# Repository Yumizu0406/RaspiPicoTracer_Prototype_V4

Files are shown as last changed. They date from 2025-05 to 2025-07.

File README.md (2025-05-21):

# RaspiPicoTracer_Prototype_V4

RaspiPicoTracerは白線の上をたどって走るロボットであり、
機能をできる限り少なくし、回路、メカ、組み立て、プログラミングなどロボット作成に必要な経験を一通り短期間で行えるように開発中です。
このロボットはマイクロマウス大会のロボトレース競技に参加することを想定して作成しています。
競技の詳細はロボトレース競技規定をご確認ください。
[ロボトレース競技規程](https://www.ntf.or.jp/?page_id=68)

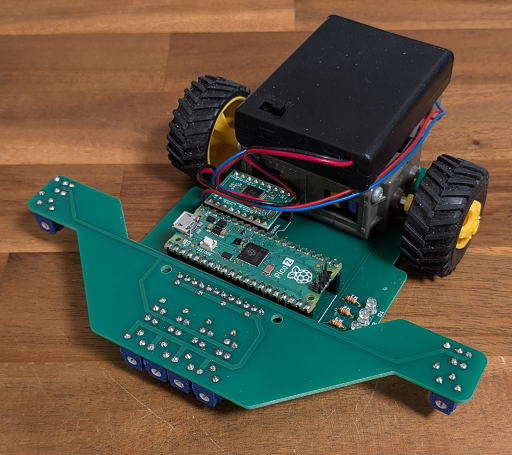
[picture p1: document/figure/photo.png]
RaspiPicoTracer_photo


<br>

# スペック
| 項目 | 詳細 |
| ---- | ---- |
| サイズ | 幅:150mm  長さ:148mm  高さ:46mm |
| 重さ | 約220g |
| 電源 | 単四電池4本 |
| モーター | FA-130 |
| モータードライバ | TB6612 |
| CPU | RP2350 |
| ラインセンサ | LBR-127HLD×4 |
| ホイール | 径:36mm 幅:16mm |

# 開発環境について
VSCodeでRaspberry Pi PicoのExtensionを使用します。
Raspberry Pi財団が公開しているドキュメント「Getting started with Raspberry Pi Pico-series」の内容に沿って行ってください。

cloneした後はImport Projectを行ってください。

# 回路図
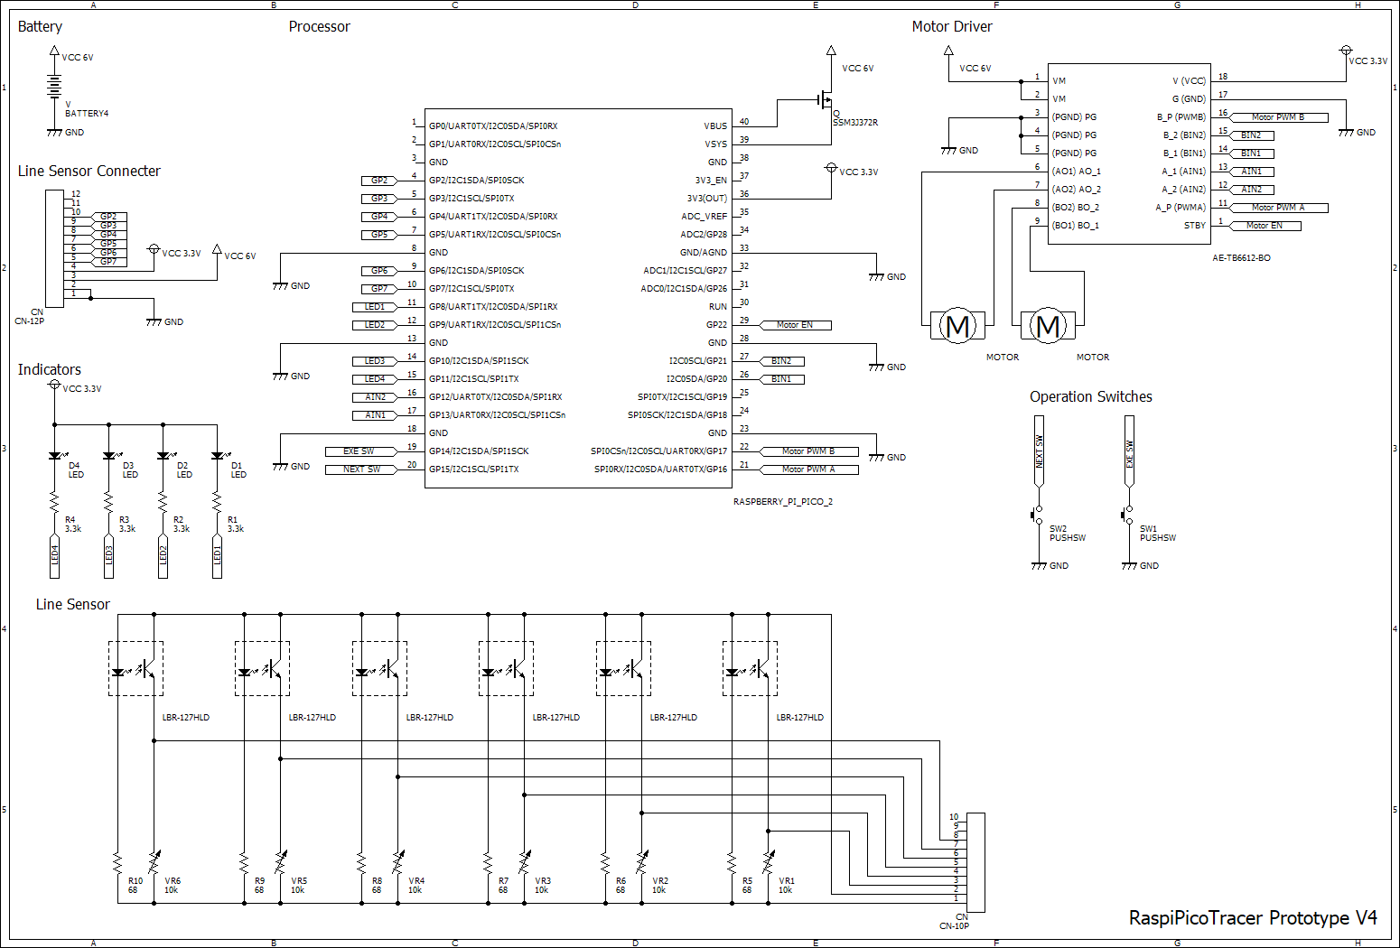
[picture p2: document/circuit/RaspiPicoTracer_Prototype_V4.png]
CircuitDiagram


# 部品表

| 名称 | メーカー | 単価 | 個数 | 備考 |
| ---- | ---- | ---- | ---- | ---- |
| メイン基板 | - | - | 1 | - |
| センサ基板 | - | - | 1 | - |
| Raspberry Pi Pico 2 | ラズベリーパイ財団 | 1000 | 1 | Raspberry Pi Picoでも可 |
| ダブルギヤボックス（左右独立４速タイプ） | 株式会社タミヤ | 924 | 1 | ギヤ比12.7:1で利用 |
| トラックタイヤセット （36mm径） | 株式会社タミヤ | 396 | 1 | - |
| 電池ボックス 単4×4本 リード線・フタ・スイッチ付 | COMFORTABLE ELECTRONIC CO., LTD(COMF) | 150 | 1 | - |
| 耐熱電子ワイヤー 黒色 20m 導体外径0.54mm(AWG24相当) | 住友電気工業株式会社 | 600 | 1 | モータードライバとモーター接続用<br>14cmのものを4つ利用 |
| TB6612モータードライバー ブレークアウトボードキット | 秋月電子 | 380 | 1 | 1 |
| LED(LC303PBL1-30Q) | - | - | 4 | 高輝度で3mm径のものならなんでもOK |
| 抵抗器 3.3kΩ | - | - | 4 | LED用 |
| ピンヘッダー 1×40 (40P) | Useconn Electronics Ltd. | 35 | 2 | - |
| 分割ロングピンソケット 1×42 (42P) | Useconn Electronics Ltd. | 80 | 2 | - |
| タクトスイッチ(DTS-63-N-V-BLK) | Cosland Co,. Ltd. | 15 | 2 | - |
| フォトリフレクター(反射型フォトセンサー) LBR-127HLD | Letex Technology Corp. | 75 | 6 | - |
| 半固定ボリューム TSR-3323S 10kΩ | SUNTAN TECHNOLOGY CO LTD | 40 | 6 | - |
| 抵抗器 68Ω | - | - | 6 | フォトリフレクター用 |

<br>

# 組み立て方法

準備として以下の工具を揃えてください。
| 名称 | 備考 |
| ---- | ---- |
| はんだごて | 15w～30wのものがよい |
| こて先クリーナー | - |
| はんだ | スズ60％ 鉛入りはんだ Φ0.8mmだとよい |
| 精密作業用ニッパー | - |
| ＋ドライバー | サイズは2番 |
| ワイヤストリッパー | あると嬉しい<br>なくてもOK |

<br>

モーターとの接続について以下の画像のように接続してください。
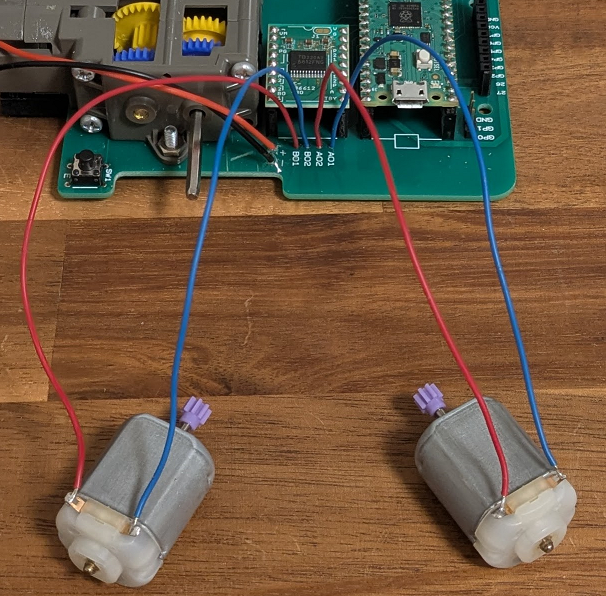
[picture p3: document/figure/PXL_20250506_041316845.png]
ConnectToMotor


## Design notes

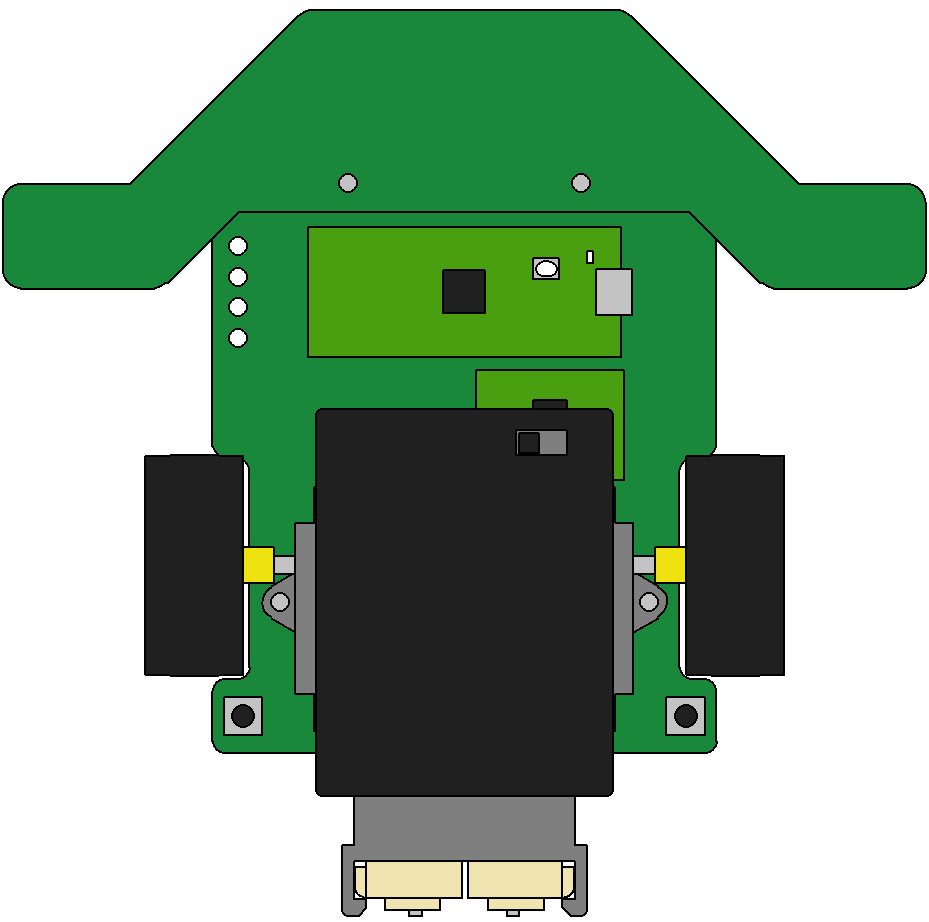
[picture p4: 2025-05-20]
document/figure/ラズピコトレーサ-.png

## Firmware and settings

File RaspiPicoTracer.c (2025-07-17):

#include <stdint.h>
#include <stdio.h>
#include "pico/stdlib.h"
#include "driver/indicators.h"
#include "driver/cycle.h"
#include "driver/sw.h"
#include "driver/lineSensor.h"
#include "driver/adchange.h"
#include "driver/TB6612FNG.h"
#include "application/control.h"
#include "application/battery_monitor.h"
#include "application/dc_motor.h"

typedef enum{
    selecting_menu = 0,
	exe_menu
}menu_status_t;

void init_driver(void);
void menu_no_0(void);
void menu_no_1(void);
void menu_no_2(void);
void menu_no_3(void);
void menu_no_4(void);
void menu_no_5(void);
void menu_no_6(void);
void menu_no_7(void);
void exe_select_func(uint8_t select_func);

static uint8_t menu_no;
static menu_status_t menu_status;

void (*ptr_f[8])(void) = {
    menu_no_0,
    menu_no_1,
    menu_no_2,
    menu_no_3,
    menu_no_4,
    menu_no_5,
    menu_no_6,
    menu_no_7
};

int main()
{
    control_parameters_t parameter;

    menu_no = 0;
    menu_status = selecting_menu;

    stdio_init_all();
    init_battery();
    init_control();

    parameter.speed_at_straight = 500;
    parameter.p_gain_at_straight = 15.0;
    set_control_parameter(trial_run, parameter);

    init_driver();
    set_speed_dc_motor(A, 1);
    set_speed_dc_motor(B, 1);

    while (true) {
        if(menu_status == selecting_menu){
            set_Raspberry_Pi_LED_mode(led_mode_switching);
            if(isSwStatus(SW_NEXT, click)){
                menu_no++;
                if(menu_no >= 8){
                    menu_no = 0;
                }
            }
            out_indicators(menu_no);

            if(isSwStatus(SW_EXE, click)){
                menu_status = exe_menu;
            }

        } else {
            set_Raspberry_Pi_LED_mode(led_mode_on);
            exe_select_func(menu_no);
        }
    }
}

void init_driver(void)
{
    init_indicators();
    init_TB6612FNG();
    init_sw();
    init_adc();
    init_lineSensor();
    init_cycle();
}

/***********************************************************************************************************************
 * Function Name: menu_no_0
 * Description  : EXEスイッチをクリックすると走行開始
 * Arguments    : none
 * Return Value : none
 ***********************************************************************************************************************/
void menu_no_0(void)
{
    if(isSwStatus(SW_EXE, click)){
        if(get_control_status() == stop){
            set_control_status(switching_to_run);
        } else {
            set_control_status(stop);
        }
    }
}

/***********************************************************************************************************************
 * Function Name: menu_no_1
 * Description  : センサー状態確認処理
 *                シリアルモニターでラインセンサーの状態が確認できる
 * Arguments    : none
 * Return Value : none
 ***********************************************************************************************************************/
void menu_no_1(void)
{
    printf("sensor = %d\n", get_line_center_deff());
    sleep_ms(500);
}

/***********************************************************************************************************************
 * Function Name: menu_no_2
 * Description  : バッテリー値状態確認処理
 * Arguments    : none
 * Return Value : none
 ***********************************************************************************************************************/
void menu_no_2(void)
{
    printf("sensor = %d\n", get_adc_value(3));
    sleep_ms(500);
}

/***********************************************************************************************************************
 * Function Name: menu_no_3
 * Description  : センサー状態確認処理
 *                シリアルモニターでラインセンサーの状態が確認できる
 *                0:黒
 *                1:白
 * Arguments    : none
 * Return Value : none
 ***********************************************************************************************************************/
void menu_no_3(void)
{
    bool *line_sensor_value;
    uint8_t line_sensor_index;

    line_sensor_value = get_line_sensor_row_value_pointer();

    for(line_sensor_index = 0; line_sensor_index < 4; line_sensor_index++){
        if(*line_sensor_value == true){
            printf("1");
        } else {
            printf("0");
        }
        line_sensor_value++;
    }
    printf("\n");
}

/***********************************************************************************************************************
 * Function Name: menu_no_4
 * Description  : モーター接続確認処理
 *                スイッチを押した側のモーターが前進する
 * Arguments    : none
 * Return Value : none
 ***********************************************************************************************************************/
void menu_no_4(void)
{
    if(isSwStatus(SW_EXE, push)){
        set_speed_dc_motor(A, 500);
    } else {
        set_speed_dc_motor(A, 0);
    }

    if(isSwStatus(SW_NEXT, push)){
        set_speed_dc_motor(B, 500);
    } else {
        set_speed_dc_motor(B, 0);
    }
}

void menu_no_5(void)
{
    if(isSwStatus(SW_EXE, click)){

    }
}

void menu_no_6(void)
{
    if(isSwStatus(SW_EXE, click)){

    }
}

void menu_no_7(void)
{
    if(isSwStatus(SW_EXE, click)){

    }
}

void exe_select_func(uint8_t select_func)
{
    (void)(*ptr_f[select_func])();
}

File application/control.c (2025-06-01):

/***********************************************************************************************************************
* ファイル名 : control.c
* 説明 : 制御モジュール
***********************************************************************************************************************/

/***********************************************************************************************************************
include
***********************************************************************************************************************/
#include "control.h"
#include "../driver/lineSensor.h"
#include "dc_motor.h"
#include "battery_monitor.h"
#include <stdint.h>

/***********************************************************************************************************************
define and const
***********************************************************************************************************************/
#define TREAD_WIDTH_MM	90
#define HALF_TREAD_WIDTH_MM TREAD_WIDTH_MM/2

/***********************************************************************************************************************
global
***********************************************************************************************************************/
static control_status_t control_status;
static run_mode_t run_mode;
static control_parameters_t parameters[run_mode_num];
static int32_t pwm_resolution;
/***********************************************************************************************************************
prototype
***********************************************************************************************************************/
void set_motor_control(int32_t speed,int16_t angular);
uint32_t calculate_pwm_duty_value_from_vattery_voltage_mV(uint16_t aim_voltage_mV);
/***********************************************************************************************************************
 * Function Name: init_control
 * Description  : 制御処理初期化処理
 * Arguments    : none
 * Return Value : none
 ***********************************************************************************************************************/
void init_control(void)
{
    control_status = stop;
    run_mode = trial_run;
    pwm_resolution = get_dc_motor_pwm_resolution();
}

/***********************************************************************************************************************
 * Function Name: set_control_parameter
 * Description  : パラメータ設定処理
 * Arguments    : none
 * Return Value : none
 ***********************************************************************************************************************/
void set_control_parameter(run_mode_t mode, control_parameters_t parameter)
{
	parameters[mode] = parameter;
}

/***********************************************************************************************************************
 * Function Name: set_run_mode
 * Description  : 走行モード設定処理
 * Arguments    : none
 * Return Value : none
 ***********************************************************************************************************************/
void set_run_mode(run_mode_t run_mode_)
{
	run_mode = run_mode_;
}

/***********************************************************************************************************************
 * Function Name: update_control
 * Description  : 制御処理更新処理
 *                1ms周期で更新されることを想定
 * Arguments    : none
 * Return Value : none
 ***********************************************************************************************************************/
void update_control(void)
{
    int16_t line_center_deff = get_line_center_deff();
    int16_t ang_control = line_center_deff * (-1);
    int32_t pwm_value_at_straight;

    update_battery();

    pwm_value_at_straight = calculate_pwm_duty_value_from_vattery_voltage_mV(parameters[run_mode].speed_at_straight);

    if(control_status == switching_to_run){
        control_status = run;
    } else if(control_status == run){
        set_motor_control(pwm_value_at_straight, ang_control);
    } else if(control_status == switching_to_stop){
        control_status = stop;
    }
}

/***********************************************************************************************************************
 * Function Name: set_control_status
 * Description  : 制御状態設定処理
 * Arguments    : none
 * Return Value : none
 ***********************************************************************************************************************/
void set_control_status(control_status_t status)
{
    control_status = status;
}

/***********************************************************************************************************************
 * Function Name: get_control_status
 * Description  : 制御状態取得処理
 * Arguments    : none
 * Return Value : none
 ***********************************************************************************************************************/
control_status_t get_control_status(void)
{
    return control_status;
}

/***********************************************************************************************************************
 * Function Name: set_motor_control
 * Description  : モーターコントロール設定処理
 * Arguments    : none
 * Return Value : none
 ***********************************************************************************************************************/
void set_motor_control(int32_t speed,int16_t angular)
{
	int control_speed_value_R;
	int control_speed_value_L;

	control_speed_value_R = speed + HALF_TREAD_WIDTH_MM * (int32_t)angular;
	control_speed_value_L = speed - HALF_TREAD_WIDTH_MM * (int32_t)angular;

    set_speed_dc_motor(Right,control_speed_value_R);
    set_speed_dc_motor(Left, control_speed_value_L);
}

/***********************************************************************************************************************
 * Function Name: calculate_pwm_duty_value_from_vattery_voltage_mV
 * Description  : 目標電圧値に応じたpwm値をバッテリー電圧値から計算する
 * Arguments    : aim_voltage_mV 目標電圧値
 * Return Value : none
 ***********************************************************************************************************************/
uint32_t calculate_pwm_duty_value_from_vattery_voltage_mV(uint16_t aim_voltage_mV)
{
	uint32_t result;
	uint16_t vattery_voltage_mV;
	uint32_t tmp_result;

	vattery_voltage_mV = get_battery_voltage_mV();

	tmp_result = (uint32_t)pwm_resolution * (uint32_t)aim_voltage_mV;
	result = tmp_result / (uint32_t)vattery_voltage_mV;

	return result;
}

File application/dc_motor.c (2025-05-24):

#include "dc_motor.h"
#include "../driver/TB6612FNG.h"

#define SHORT_MAX 65535

/***********************************************************************************************************************
 * Function Name: init_dc_motor
 * Description  : dc_motor初期化処理
 * Arguments    : none
 * Return Value : none
 ***********************************************************************************************************************/
void init_dc_motor(void)
{
}

/***********************************************************************************************************************
 * Function Name: set_speed_dc_motor
 * Description  : モーター速度設定処理
 * Arguments    : ch モーターのチャンネル
				  speed 速度
 * Return Value : none
 ***********************************************************************************************************************/
void set_speed_dc_motor(DC_MOTOR_CH ch, int32_t speed)
{
	int32_t speed_int_abs;
	TB6612FNG_CH TB6612FNG_ch;

	if(ch == Right){
		TB6612FNG_ch = B;
	} else {
		TB6612FNG_ch = A;
	}

	if(speed < 0){
		speed_int_abs = -1 * speed;
	} else {
		speed_int_abs = speed;
	}

	if(SHORT_MAX < speed_int_abs){
		speed_int_abs = SHORT_MAX;
	}

	if(0 <= speed){
		if(ch == Right){
			set_control(TB6612FNG_ch,CW);
		} else {
			set_control(TB6612FNG_ch,CW);
		}
	} else {
		if(ch == Right){
			set_control(TB6612FNG_ch,CCW);
		} else {
			set_control(TB6612FNG_ch,CCW);
		}
	}
	set_pwm_value(TB6612FNG_ch,(uint16_t)speed_int_abs);
}

/***********************************************************************************************************************
 * Function Name: get_dc_motor_pwm_resolution
 * Description  : PWM分解能取得処理
 * Arguments    : none
 * Return Value : 分解能
 ***********************************************************************************************************************/
uint16_t get_dc_motor_pwm_resolution(void)
{
	return get_pwm_resolution();
}

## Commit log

2025-05-20 ドキュメントに使うファイル追加
2025-05-20 README.md追加
2025-05-21 写真追加
2025-05-21 README.mdに写真追加
2025-05-21 外部リンクを更新
2025-05-21 部品表更新
2025-05-24 ガーバデータ追加
    [RaspiPicoTracerPV4.GBL, RaspiPicoTracerPV4.GBS, RaspiPicoTracerPV4.GTL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]
2025-05-24 ソースコミット
2025-05-31 バッテリー処理追加
2025-06-01 AD変換の不具合を修正およびバッテリーの電圧値の計算とトリム移動平均の処理を追加
2025-06-01 モーター出力をバッテリー値から算出する処理を追加
2025-07-17 モーター用のテストモード追加
